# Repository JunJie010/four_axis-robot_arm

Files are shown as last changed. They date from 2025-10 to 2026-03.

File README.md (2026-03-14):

# 基于ESP32的四轴机械臂
>本项目基于**小智&阿奇联合出品 海豚机械臂**开源学习
>
>原项目地址：[机械臂数字孪生项目](https://x509p6c8to.feishu.cn/docx/FeMndRrzRommxGxTkFscJ0zKnKh)
>
>在此感谢原项目作者小智，阿奇的杰出工作
## 项目预览
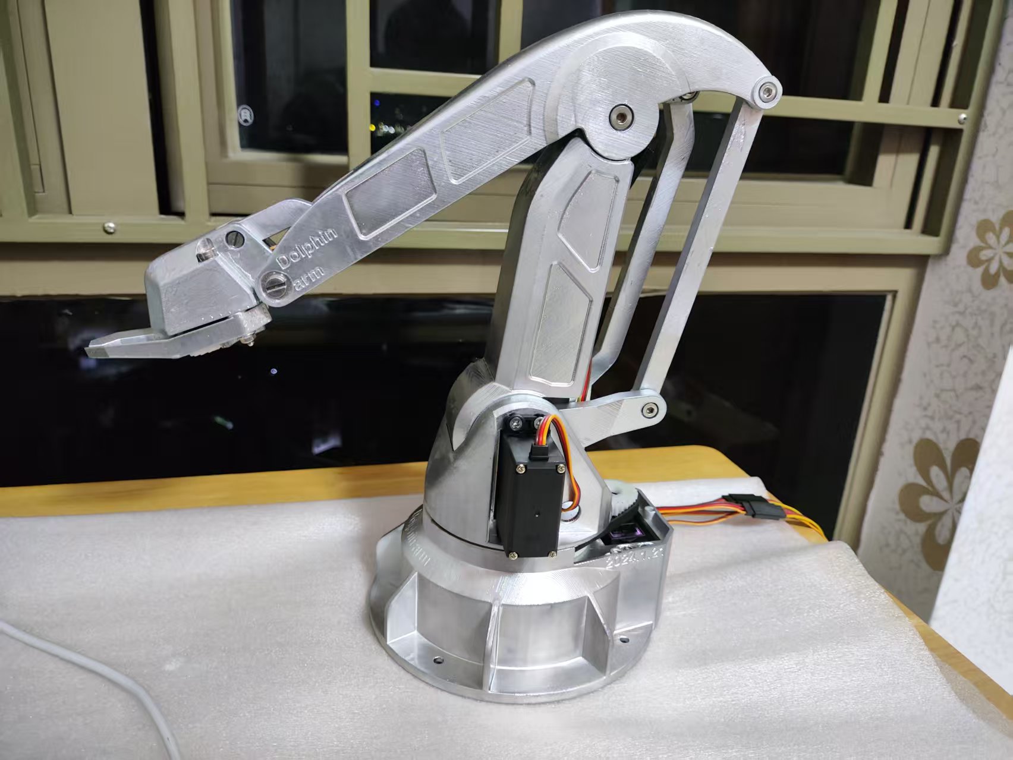
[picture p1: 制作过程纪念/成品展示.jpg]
项目展示

[点击下载项目演示视频](https://github.com/JunJie010/four_axis-robot_arm/blob/main/%E5%88%B6%E4%BD%9C%E8%BF%87%E7%A8%8B%E7%BA%AA%E5%BF%B5/%E6%88%90%E5%93%81%E5%B1%95%E7%A4%BA.mp4)

## 项目功能

- **手机蓝牙遥控**  
  基于 BLE 低功耗蓝牙协议，可通过手机 APP 连接机械臂，实现四轴关节的独立控制和夹爪开合，控制距离满足桌面级应用需求。

- **多舵机协同运动**  
  机身采用 3 个 MG996R 舵机驱动大臂、小臂和底座旋转，夹爪采用 SG90 舵机，通过自定义定时器调度算法实现多舵机同步运动，并可调节转动速度。

- **精确角度控制**  
  基于正逆运动学算法，将机械臂末端位置映射为各关节舵机角度，支持点到点运动控制，可完成指定位置的抓取与释放任务。

- **夹爪抓取功能**  
  夹爪采用双齿轮对称结构设计，最大抓取直径约 3cm，可轻松夹取积木、螺丝等小型物件，夹取力度适中，成功率超过 83%。

- **结构巧妙设计**  
  从零进行机械结构设计，包含固定底座、旋转底座、平行四边形连杆机构和夹爪模块，全部零部件通过 3D 打印制作并手工组装。

## 项目职责
* 设计机械臂结构，包括**固定底座，旋转底座，连杆机构，夹爪机构**
* 3D打印零部件，并进行机械组装
* 绘制主控板，包括**供电，控制器，串口，排针等等**
* 编写机械臂控制代码，包括**舵机驱动代码，蓝牙模块代码**
* 机械臂运动学算法，**正逆运算**
***
## 关于主控板绘制
### 原理图设计如下
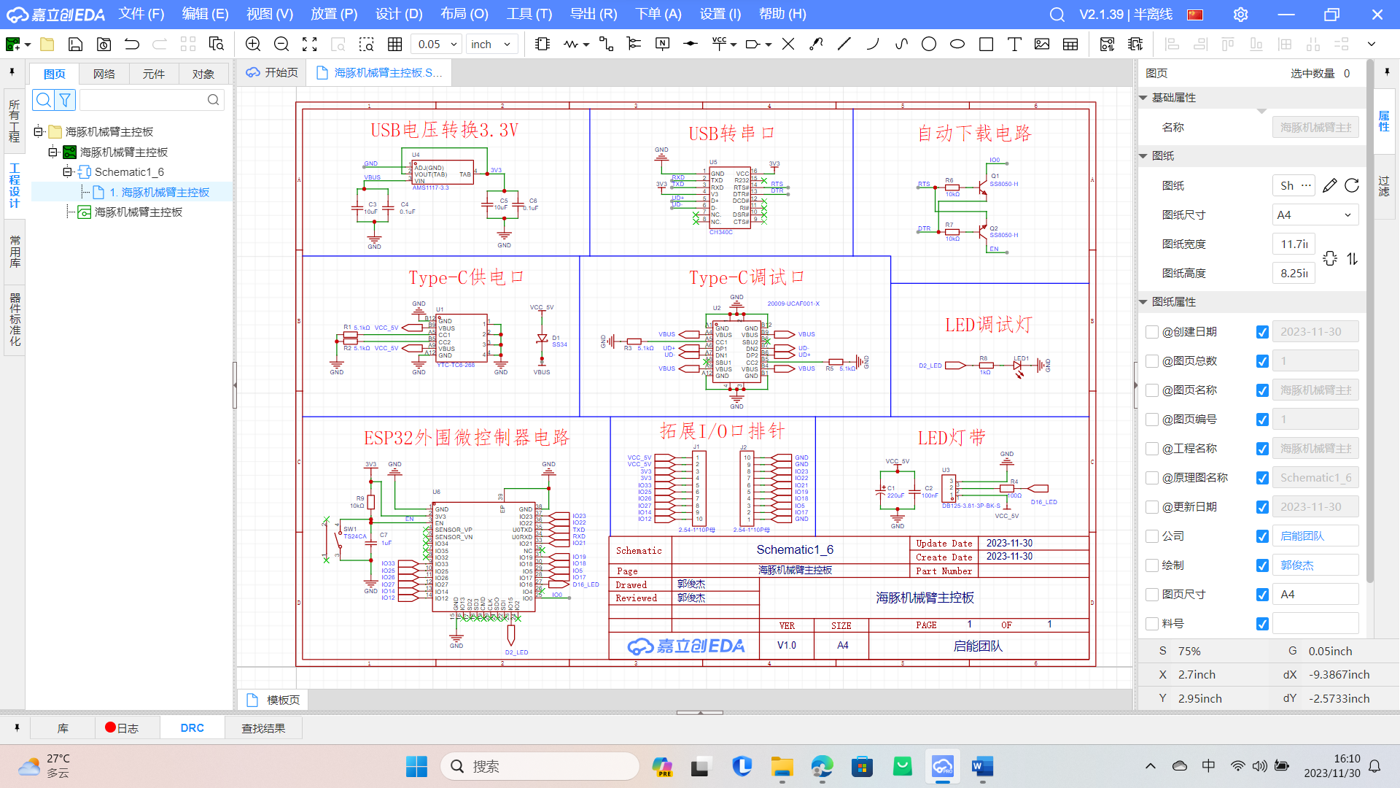
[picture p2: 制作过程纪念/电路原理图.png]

### PCBlayout
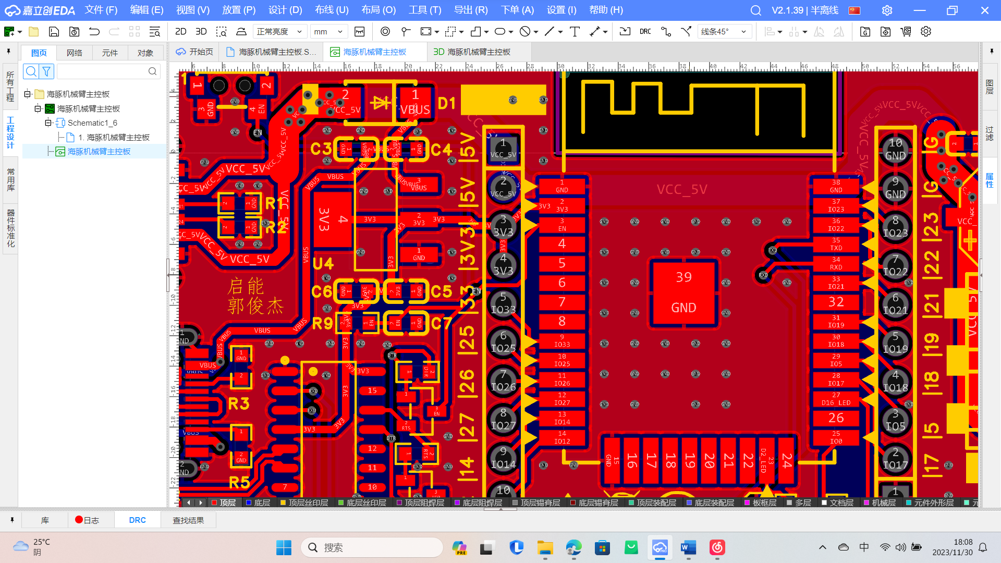
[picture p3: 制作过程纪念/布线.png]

### 板子查看
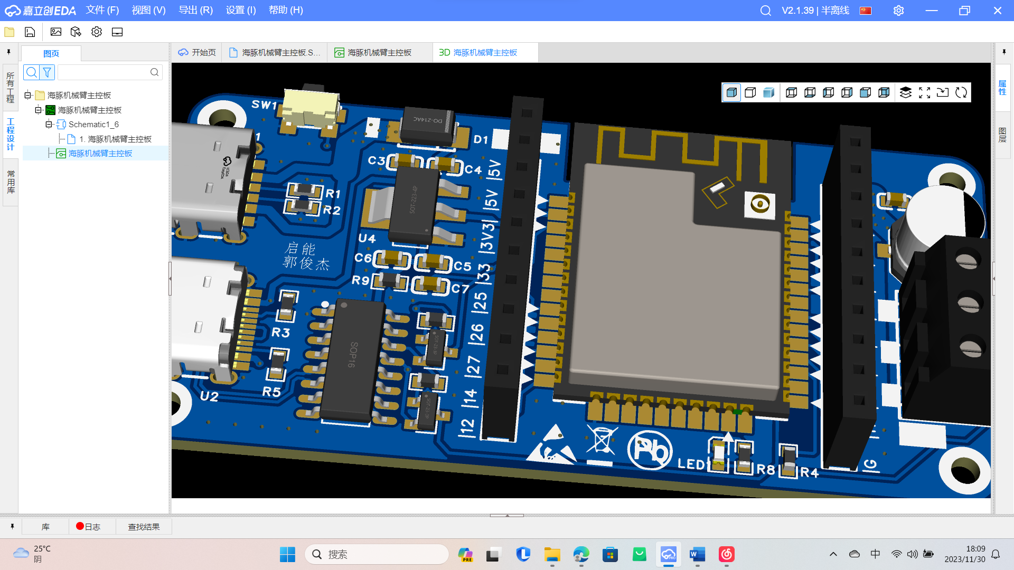
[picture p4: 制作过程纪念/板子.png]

***
## 关于控制代码的编写
编写Arduino，开发环境为VScode，下载PlatformIO插件，用于标准库开发ESP32项目
### 舵机驱动控制
机身采用3个MG996R舵机，夹爪采用SG90舵机，舵机的驱动原理是发送PWM信号，通过改变占空比驱动舵机的转动角度

PWM(Pulse Width Modulation)脉冲宽度调制，在具有惯性的系统中，可以通过一系列脉冲的宽度进行调制，来等效的获得所需模拟参量，常应用于电机控速领域

常用调制方法为通过定时器输出比较功能，通过设置PSC，ARR，CCR寄存器的值来调制一个频率可调，占空比受CCR控制的PWM波形

此处由于引入了ESP32Servo标准库，可以直接用舵机标准库函数对舵机角度进行控制
```      
#include <ESP32Servo.h>               //引入舵机标准库函数

Servo servo;                          //定义舵机变量
servo.setPeriodHertz(50);             //舵机频率初始化函数;
servo.attach(servo_pin,500,2500);     //舵机的初始化参数配置，已对引脚进行配置,参数为引脚，最小微秒，最大微秒
servo.write(45);                      //舵机角度控制函数,参数为舵机角度
//注意，此处只做简单展示，详细代码请看控制代码
```
单舵机的控制较为简单，引入多舵机后需要分别控制各个舵机的角度，可以利用定时器定时功能，每隔一段时间进行一次角度判断函数，当舵机的set和now不同时，舵机转动，并且每转动一次对now加以修正
所以只需要对set值修改就可以驱动舵机转动到相应角度，同时，定时器计时频率可以改变舵机的转动速度，实现多舵机的速度控制
```           
#include <Ticker.h>              //引入定时器功能

struct SERVO                     //定义舵机结构体
{
    Servo engine[4];             //定义舵机变量参数
    uint8_t now[4];              //定义舵机当前角度参数   
    uint8_t set[4];              //定义舵机设置角度参数
};
SERVO servo_engine;              //定义舵机结构体变量
Ticker timer;                    //定义定时器变量

void Servo_Init()                //定义舵机初始化函数，对舵机频率初始化，参数引脚初始化
void Servo_back()                //定义舵机归位函数，机械设计时设计每个舵机的初始值，上电后自动执行复位功能
void timer_speed(uint8_t x)      //舵机速度控制函数，原理是利用定时器定时功能，每隔一段时间进行一次角度判断函数
void timer_back()                //定义舵机now修正函数，在舵机运动到指定位置后，修正now为当前值，避免一直运动
uint8_t Servo_run(uint8_t x,uint8_t set_angle,uint8_t now_angle)         //定义舵机驱动函数，当set和now不同时，舵机驱动
void Servo_motor_run(uint8_t a,uint8_t b,uint8_t c,uint8_t d)         //定义多舵机控制函数，给set值
//注意，此处只做简单展示，详细代码请看控制代码
```
### 多舵机控制
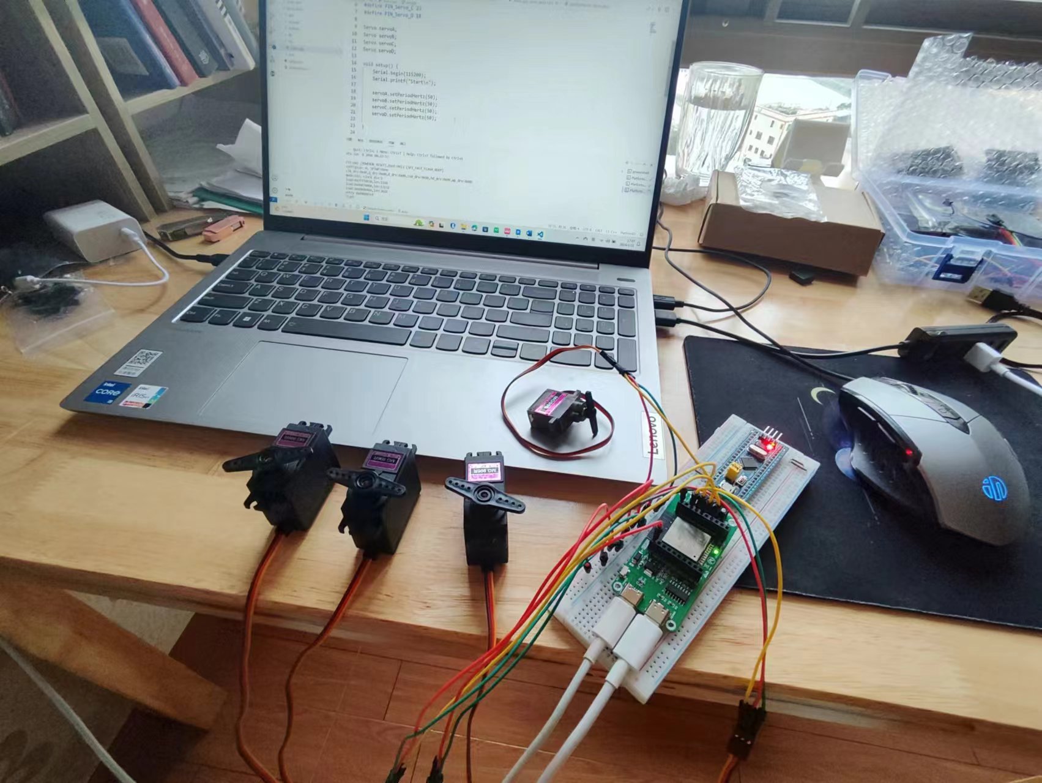
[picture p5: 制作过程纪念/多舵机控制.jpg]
舵机控制

### 蓝牙模块编写
采用蓝牙模块，由于项目与控制端距离近，控制方便简单，故此处采用BLE(低功耗蓝牙)
在BLE通信模式中，存在两类设备：BLE服务端和BLE客户端，通信时，BLE服务端向外发送信号，可以被附件BLE客户端发现，一个BLE客户端可以连接特定的服务端，然后读取服务端发送的信号数据
BLE不但支持点对点传输，还支持广播模式，还可以组建Mesh网络
```
#include <BLEDevice.h>
#include <BLE2902.h>              //引进相关蓝牙通讯协议

#define SERVICE_UUID "4fafc201-1fb5-459e-8fcc-c5c9c331914b"
#define CHARACTERISTIC_UUID "beb5483e-36e1-4688-b7f5-ea07361b26a8"       //完整的128位UUID码

BLECharacteristic *pCharacteristic = NULL;            //创建特征Characteristic
bool bleConnected = false;                            //定义布尔型变量用于判断蓝牙是否连接

class bleServerCallbacks : public BLEServerCallbacks                     //Server回调函数声明，并用串口打印设备的连接状况
class bleCharacteristicCallbacks : public BLECharacteristicCallbacks      //客户端回调函数声明，用于客户端读取事件和写入事件
void BLE_Init()                   //定义初始化蓝牙函数，创建BLE蓝牙设备，创建服务器，设置设备的模式为BLE Server，创建服务，启动服务并开启广播
//注意，此处只做简单展示，详细代码请看控制代码
```
### 手机蓝牙控制
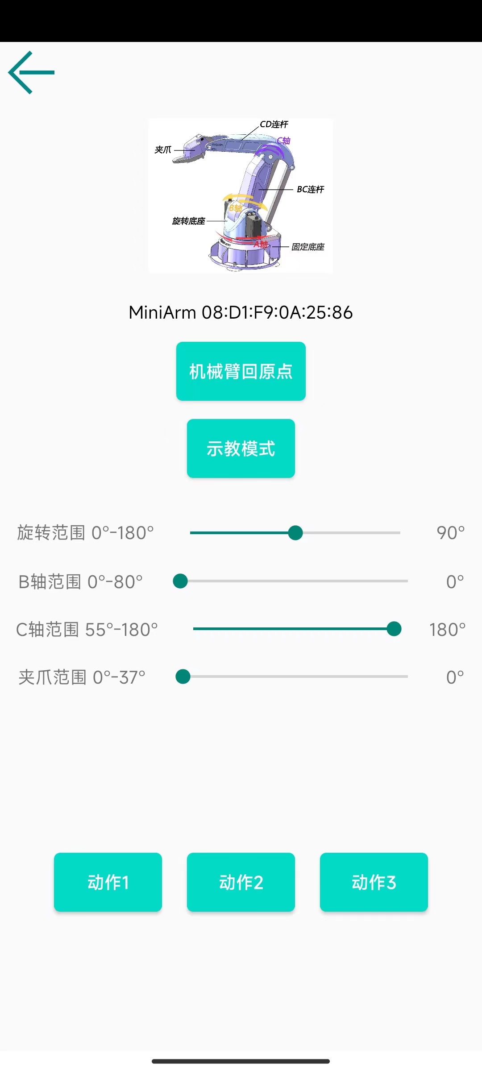
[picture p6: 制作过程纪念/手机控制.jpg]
蓝牙编写

***
## 关于运动学算法
由于机械臂机械设计结构原因，舵机无法实现自由转动，受到结构限制

此处采用正逆运算解决运动学问题，正向运动学：给定机器人各关节变量，计算机器人末端的位置姿态，逆向运动学：已知机器人的末端位置姿态，计算机器人各关节的变量
假设各轴角度为A,B,C,D；各舵机角度为A_,B_,C_,D_；

通过机械结构和正逆运算，得到以下结论
>A轴：
>
>0 < A_ < 180; 0 < A < 70; A = A_ / (72/28)
>
>B轴：
>
>0 < B_ < 80; 0 < B < 80; B = B_
>
>C轴：
>
>140 - B_ < C_ < MIN(180,196-B_); 43.5 < C < MIN(83.5,95.5); C = B + C_ -96.5
>
>D轴：
>
>0 < D_ < 37.5; 0 < G < 29; G = G_/(22/17)

***
## 关于结构设计
逆向工业型机械臂ABB-irb-460，得出机械臂运动原理，是由两个平行四边形的连杆机构使得D轴始终与地面垂直，确定了设计框架
### 逆向工程
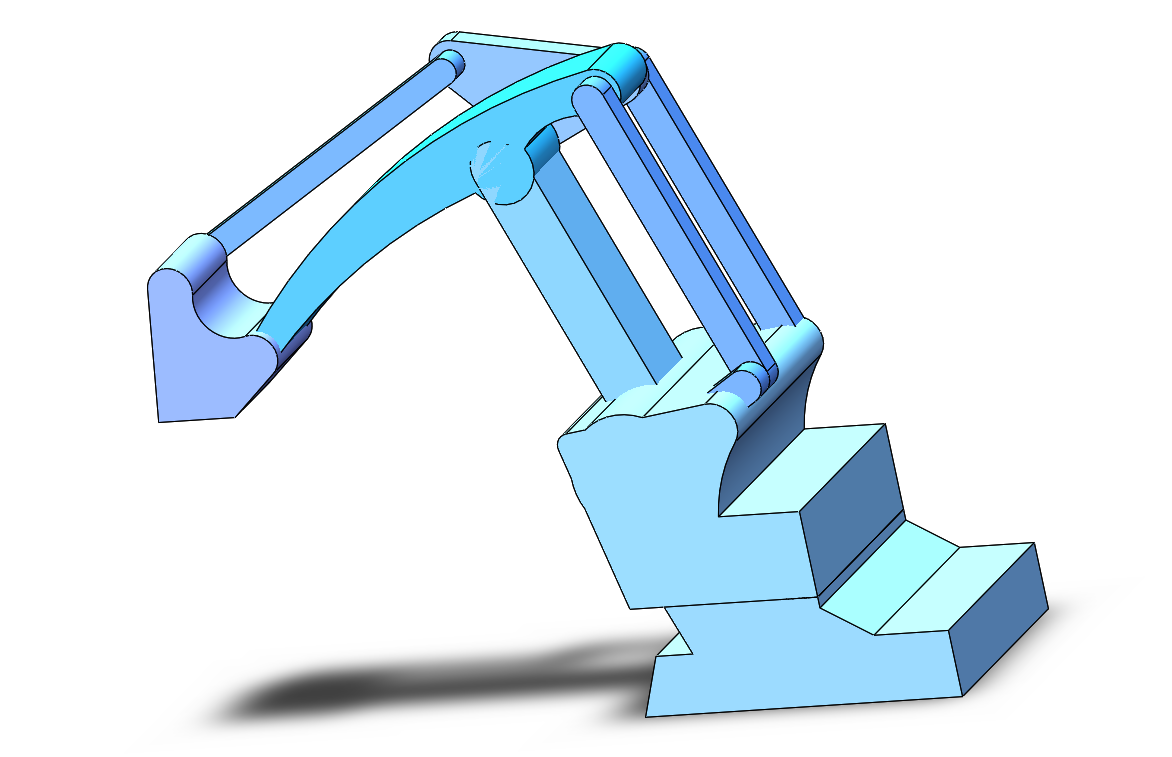
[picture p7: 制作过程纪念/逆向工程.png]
逆向工程

### 平行四边形法则
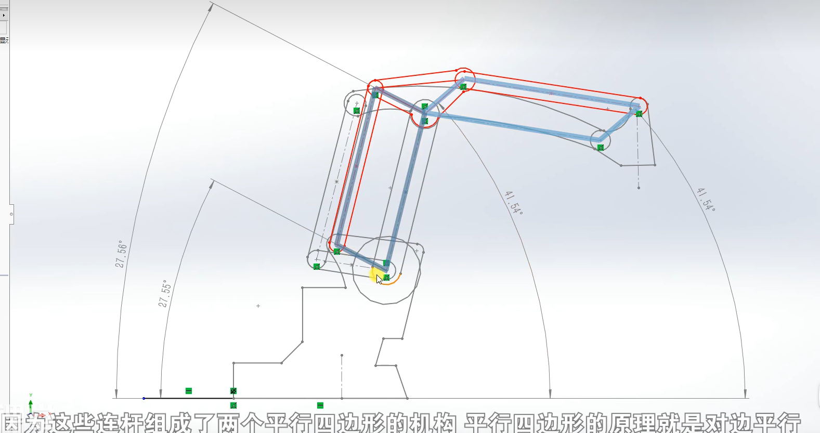
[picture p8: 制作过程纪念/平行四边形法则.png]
机械原理

### A轴 固定底座设计
>**需求：**
>
>旋转机构，将舵机安装在固定底座内，设计它们之间的驱动，考虑如何将舵机线通过A轴
>
>**解决：**
>
>轴承的外圈固定在固定底座上，轴承的内圈与旋转底座相连；
>大同步带轮与小同步带轮之间通过同步带驱动；
>用轴间螺丝，防松螺母将两个轴承连接起来；
>在大轴承的内部设计一个过线孔；
>
### A轴 固定底座预览
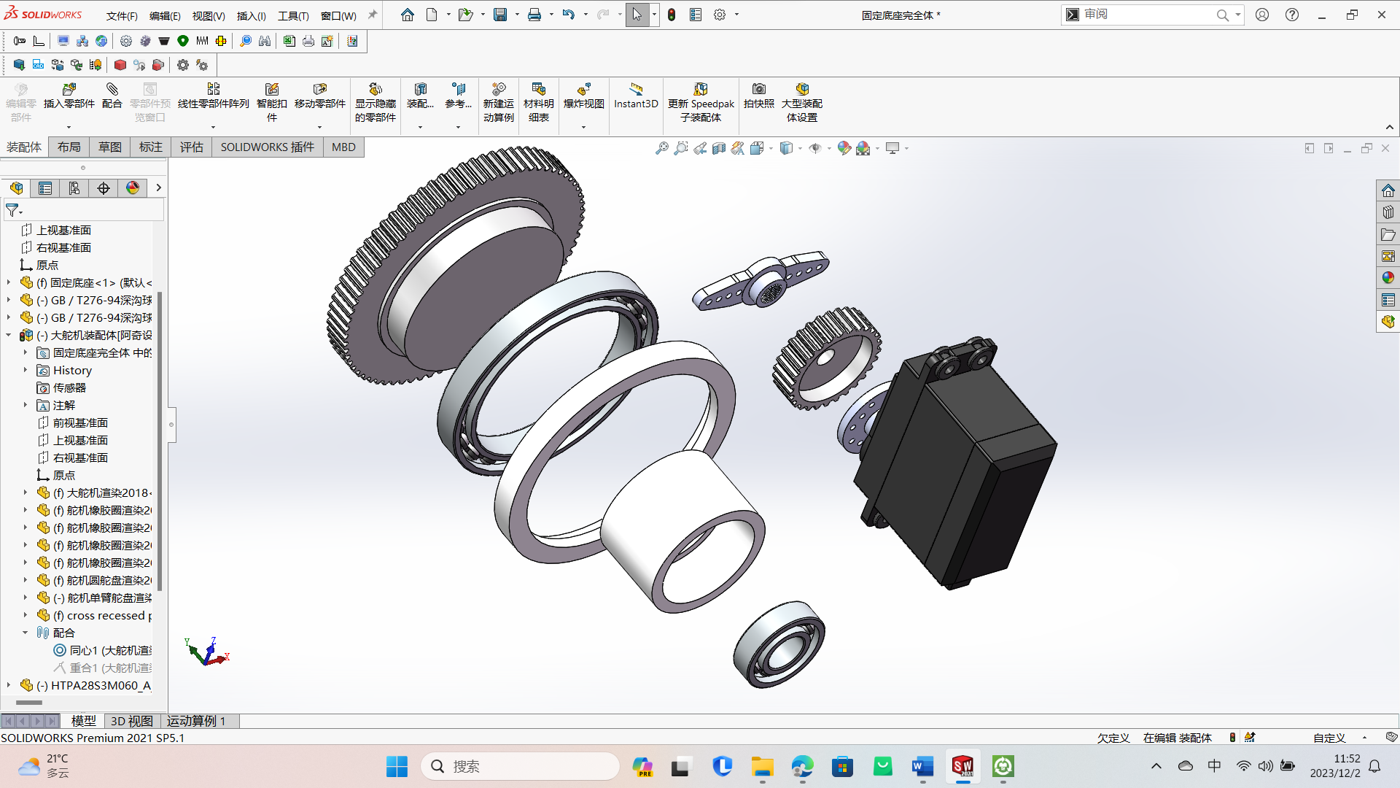
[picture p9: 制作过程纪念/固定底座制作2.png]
固定底座

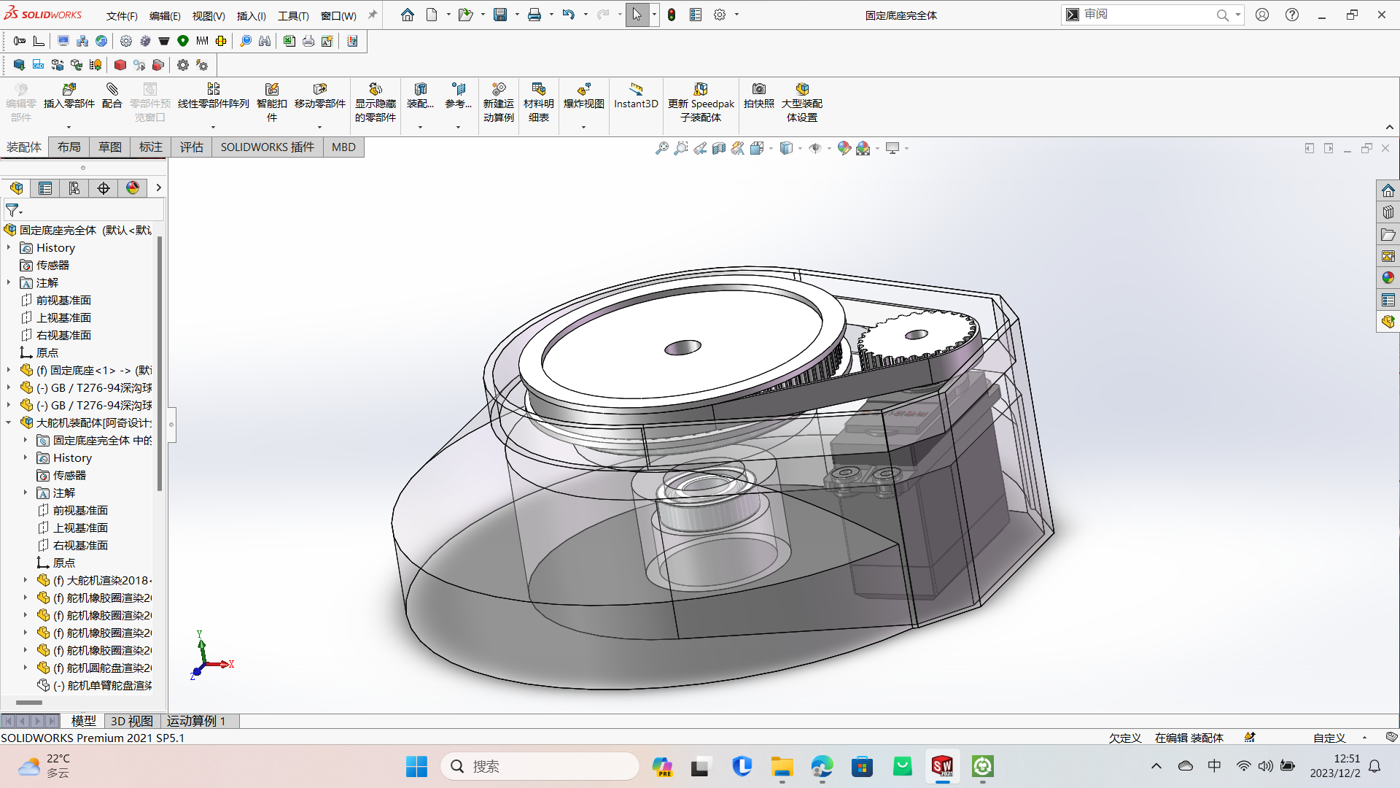
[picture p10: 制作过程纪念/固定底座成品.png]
固定底座

### B轴 旋转底座设计
>**需求：**
>
>旋转底座与固定底座连接，舵机如何驱动BC连杆与C轴连杆，BC连杆与C轴连杆的旋转机构，舵机如何安装
>
>**解决：**
>
>采用螺丝或螺母连接；
>C轴摇杆驱动，圆舵盘直连；
>BC连杆驱动需要一定的刚性，设计为一字舵盘连轴器；
>深沟球轴承，螺丝与螺母固定，BC连杆采用双臂结构以增加刚性；
>
### B轴 旋转底座预览
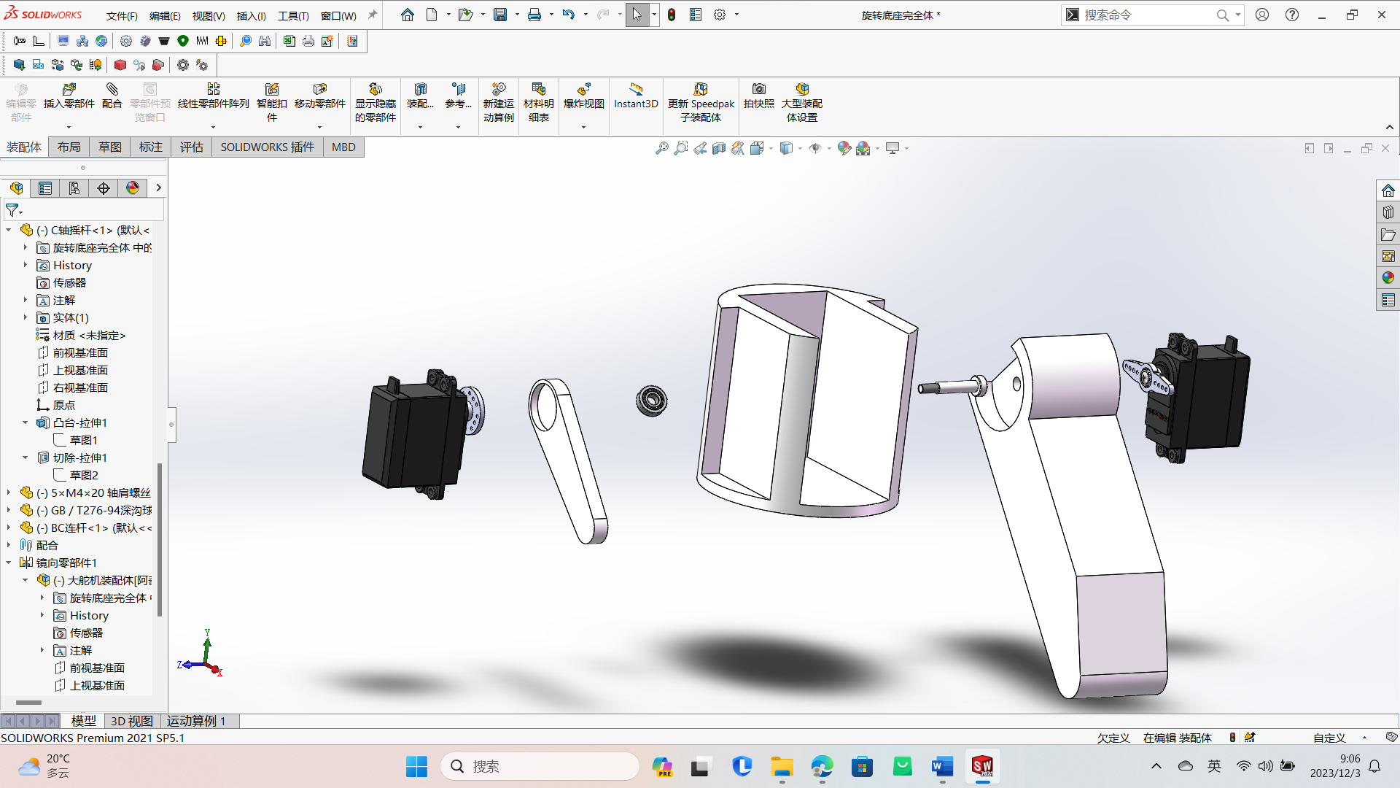
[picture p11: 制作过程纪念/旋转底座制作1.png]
旋转底座

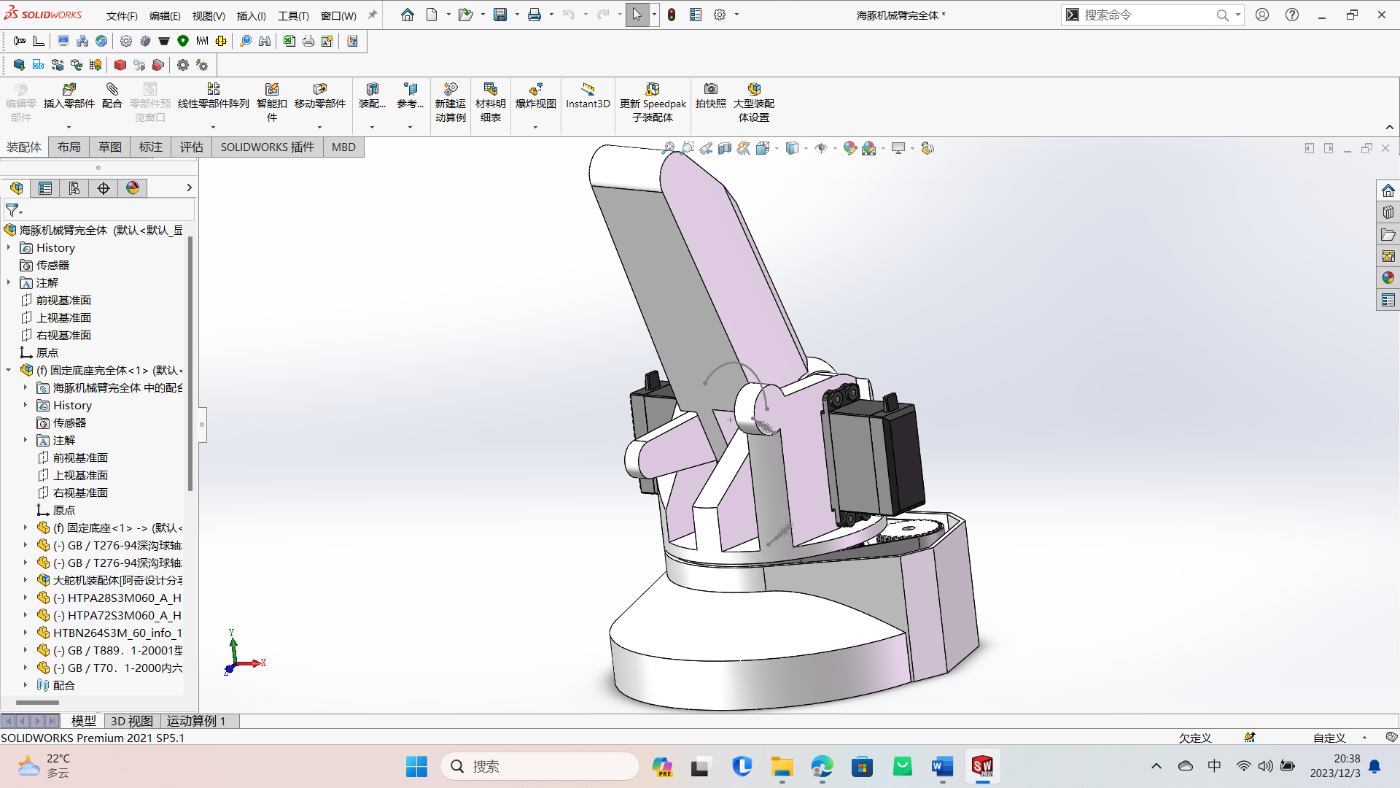
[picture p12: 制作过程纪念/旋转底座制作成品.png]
旋转底座

### 旋转底座中枢机构比较复杂，容易报错，需细心处理
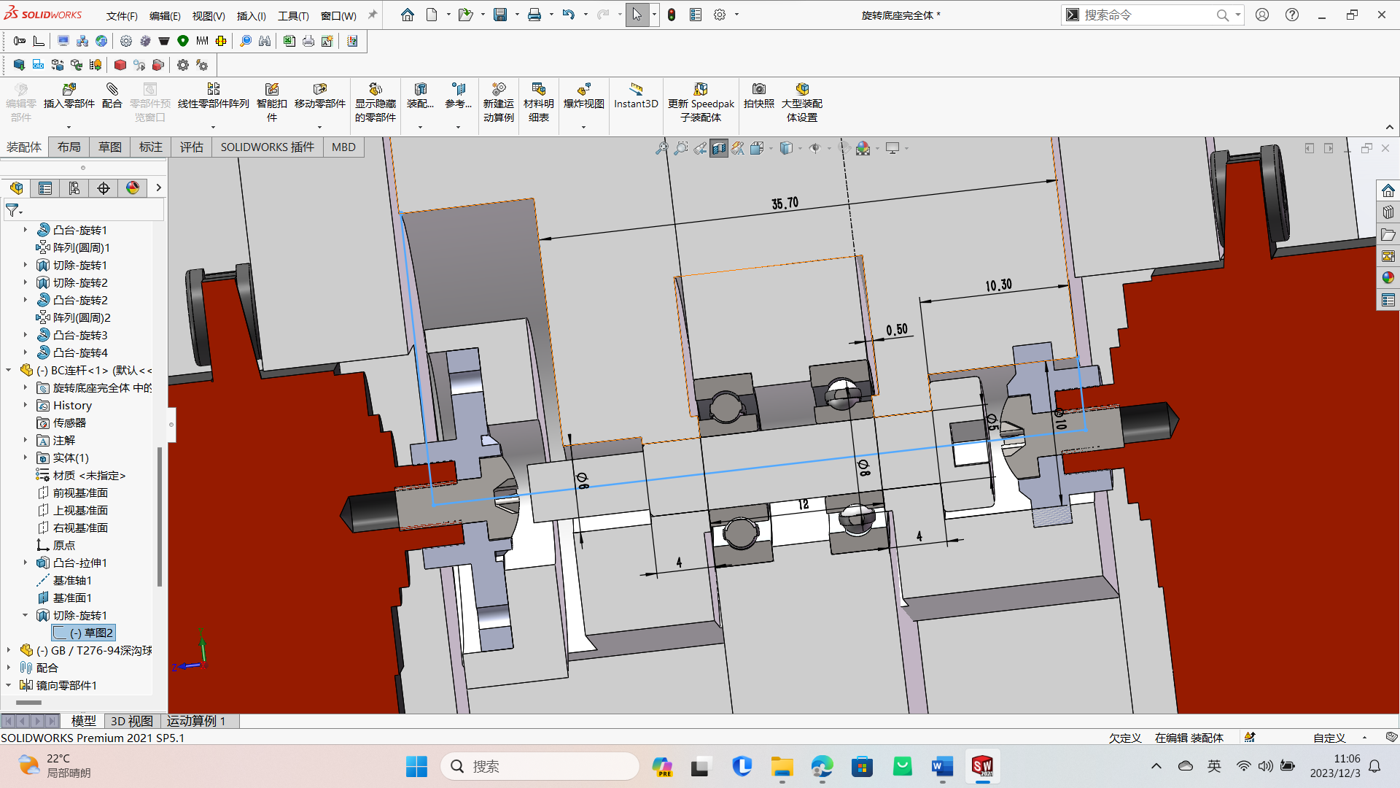
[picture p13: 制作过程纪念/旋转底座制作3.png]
旋转底座

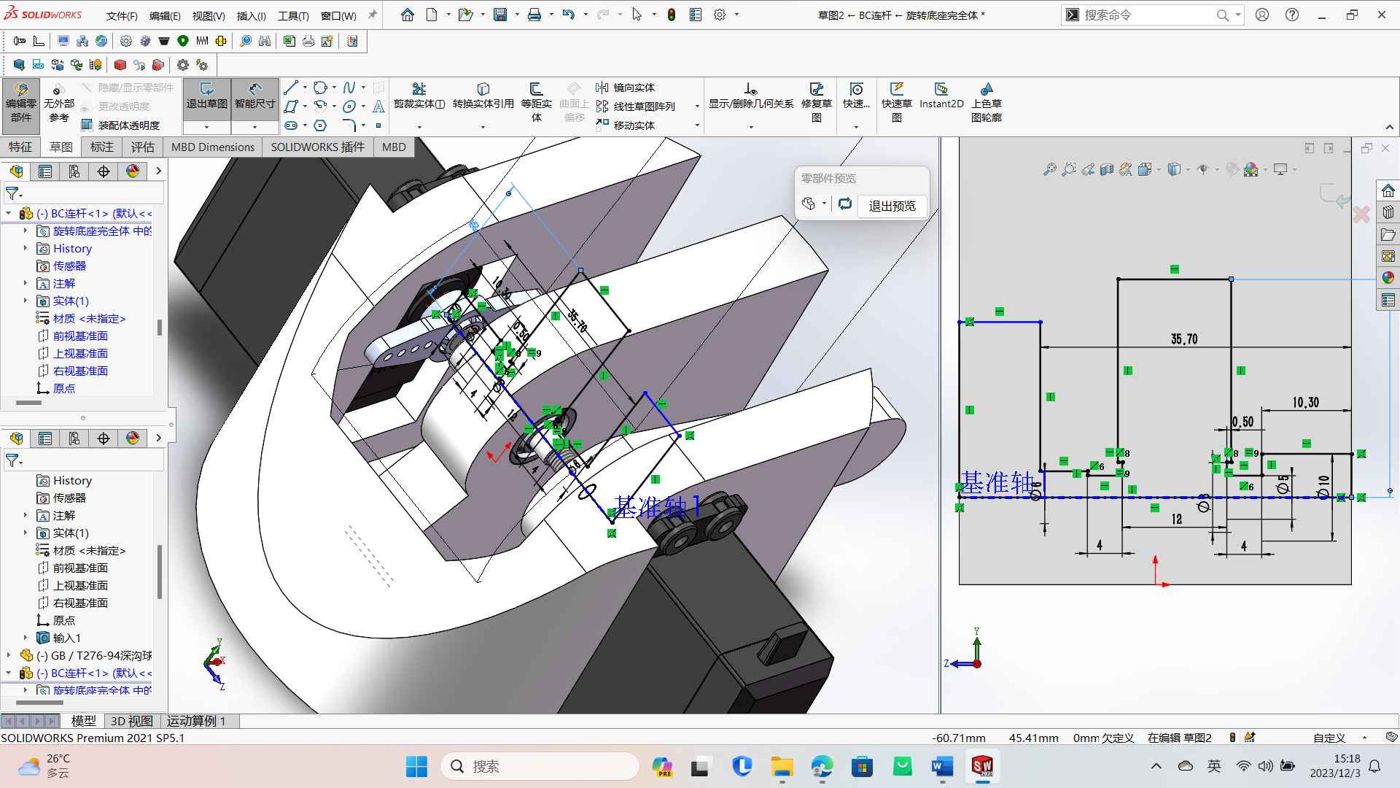
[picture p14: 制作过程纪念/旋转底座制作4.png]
旋转底座

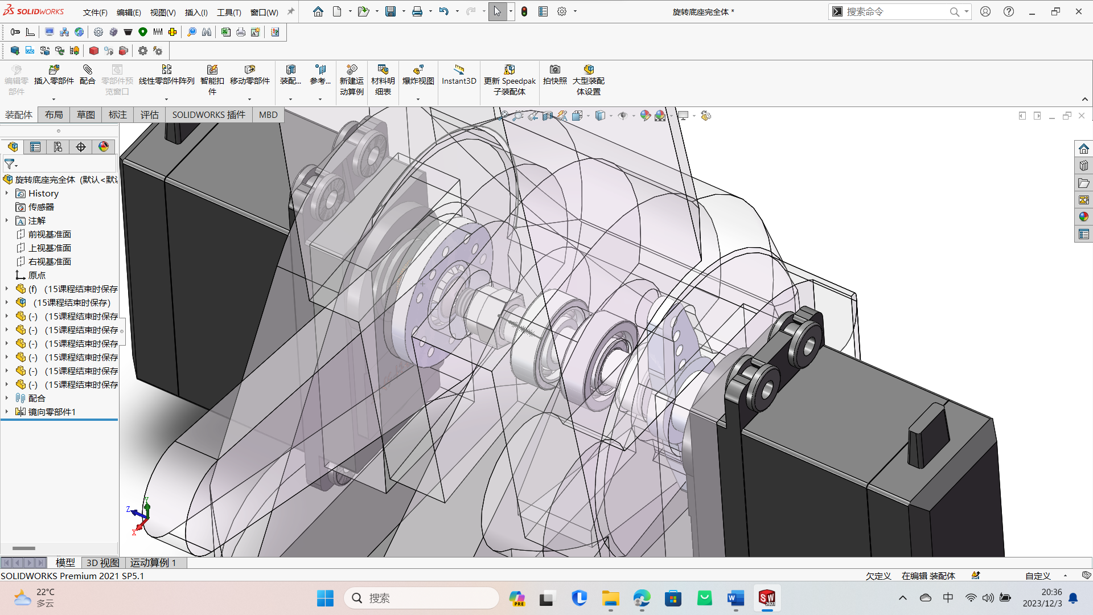
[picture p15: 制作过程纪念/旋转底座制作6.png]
旋转底座

### C轴部分 连杆机构
>**需求：**
>
>CD连杆，三角形连杆的外形尺寸，C轴机构的设计，BC，CD，三角形连杆之间的配合，连杆之间的旋转机构
>
>**解决：**
>
>采用平行四边形结构
>
### C轴 连杆机构预览
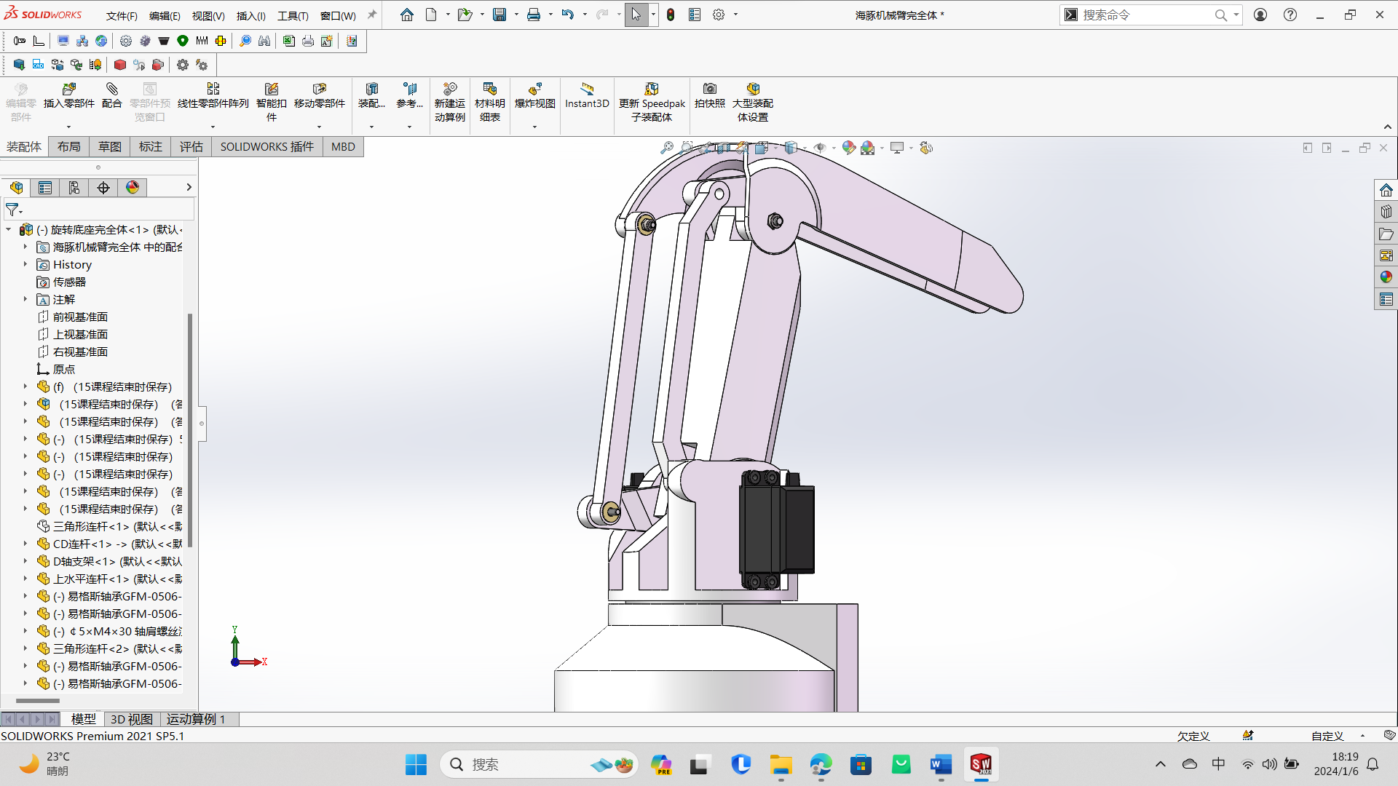
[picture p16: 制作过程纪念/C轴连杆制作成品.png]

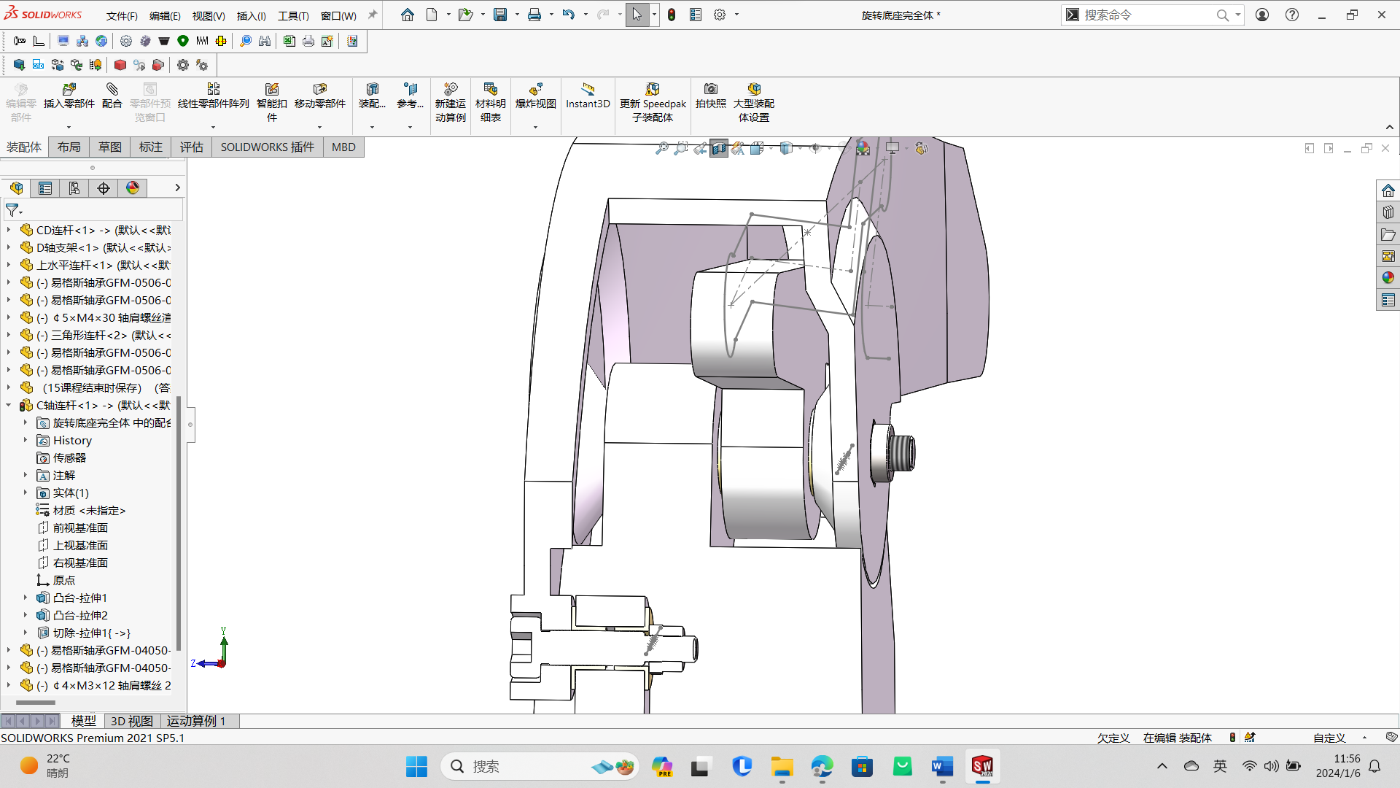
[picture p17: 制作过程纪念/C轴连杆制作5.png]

### 连杆机构中枢机构比较复杂，容易报错，需细心处理
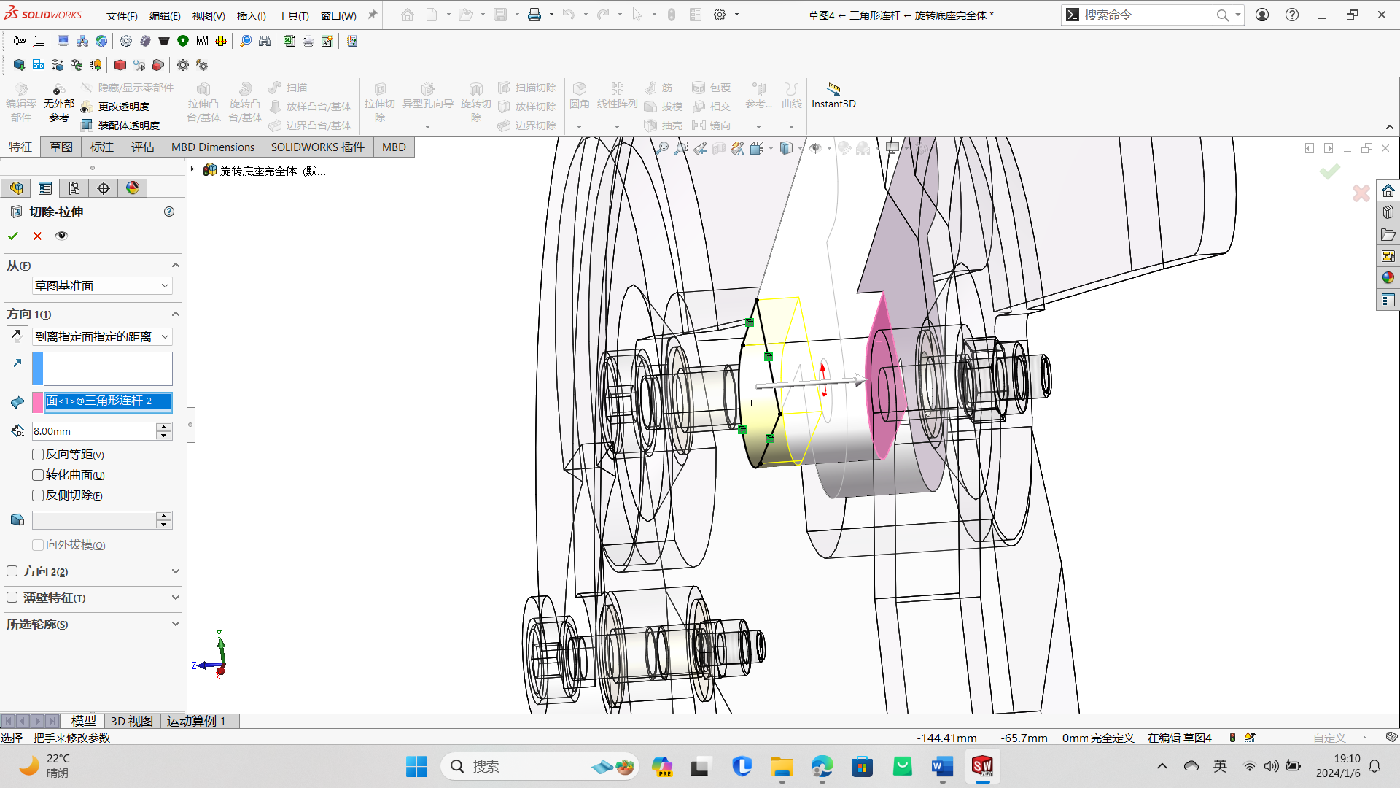
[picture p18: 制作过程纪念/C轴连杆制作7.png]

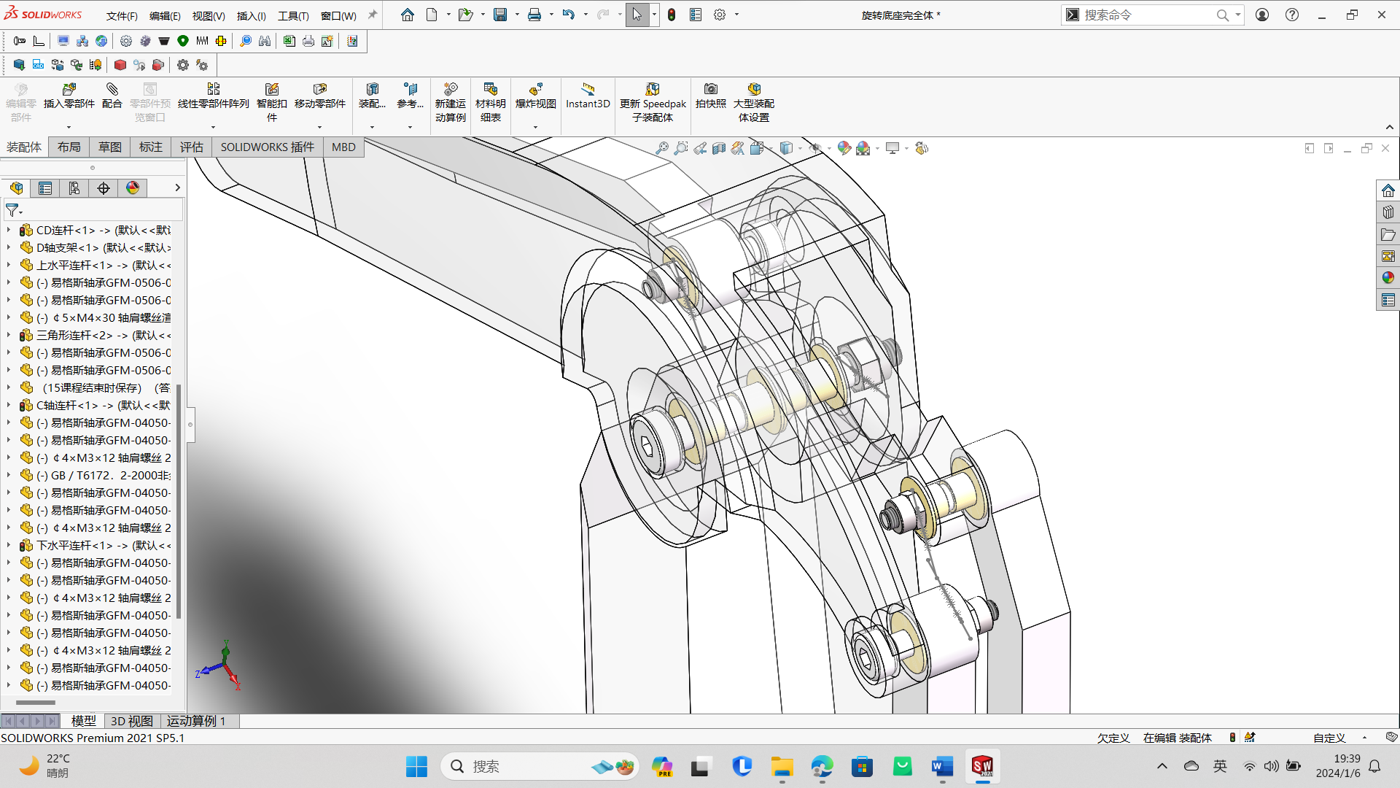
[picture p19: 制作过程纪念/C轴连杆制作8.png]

### D轴部分 夹爪机构
>**需求：**
>
>夹爪与CD连杆，上水平连杆之间的连接，能夹取一些放置在桌面的小物品，能夹多大的，夹取动作结构，动力来源
>
>**解决：**
>
>动力来源采用双齿轮结构；
>夹取方式为旋转手指，对称结构；
>夹取直径大概3cm左右；
>
### D轴部分 夹爪机构预览
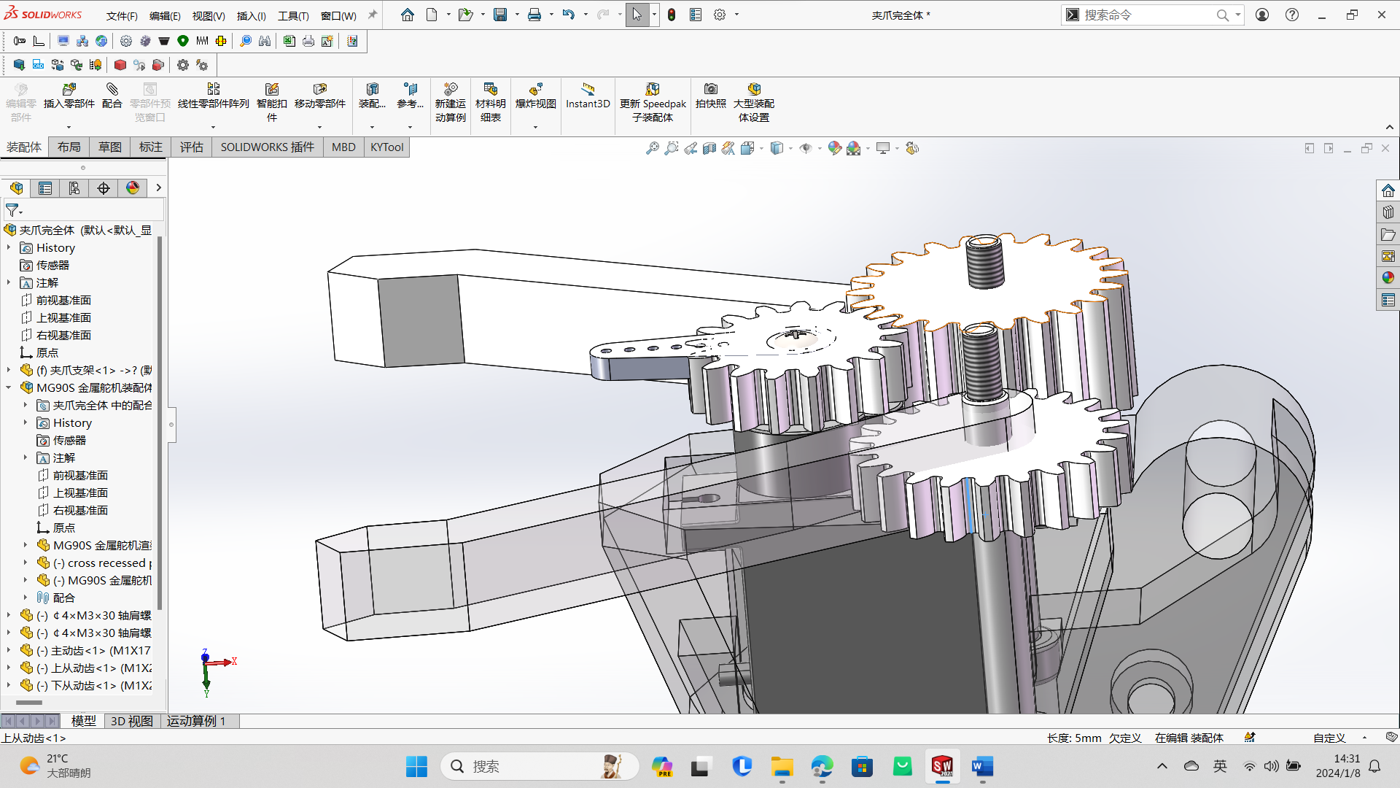
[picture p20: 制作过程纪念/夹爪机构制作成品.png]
夹爪机构

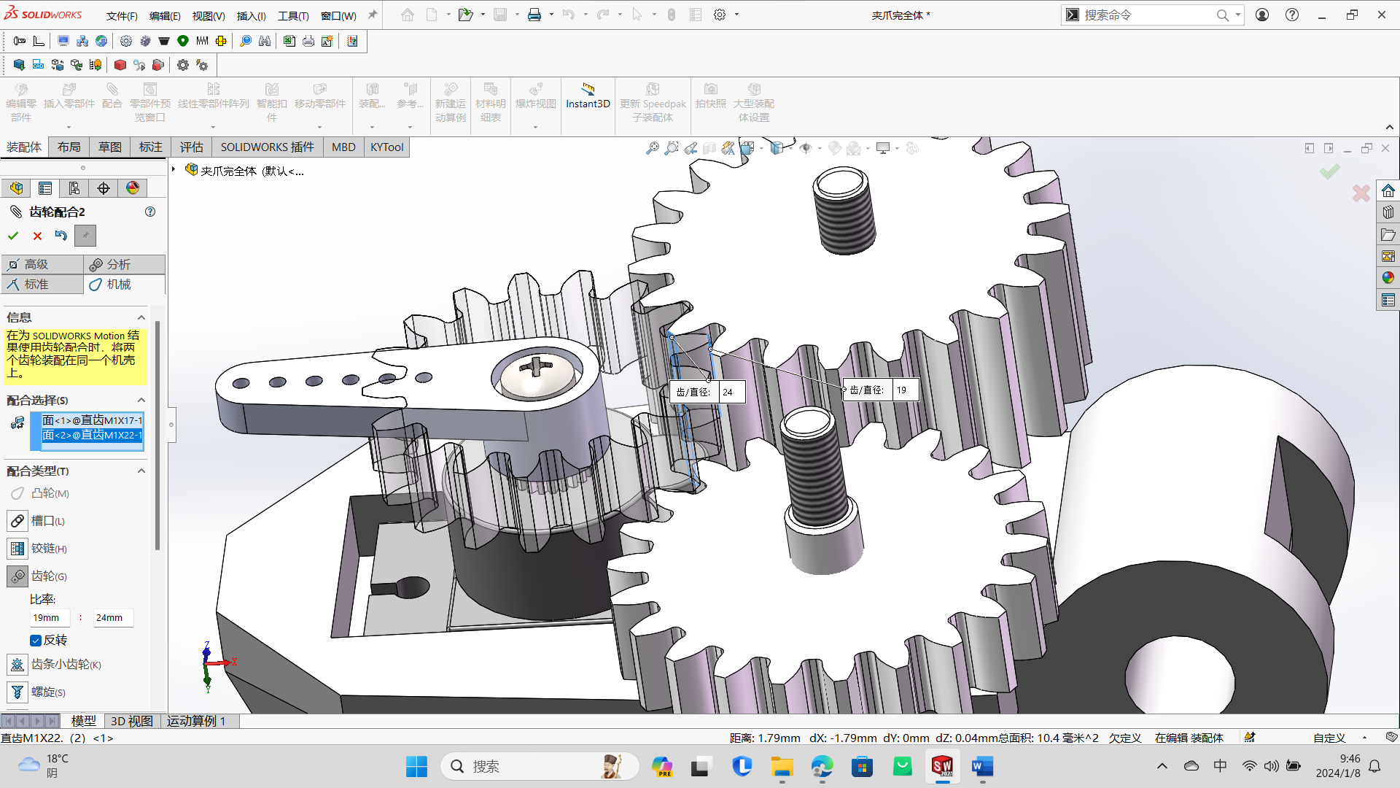
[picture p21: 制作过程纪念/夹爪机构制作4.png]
夹爪机构

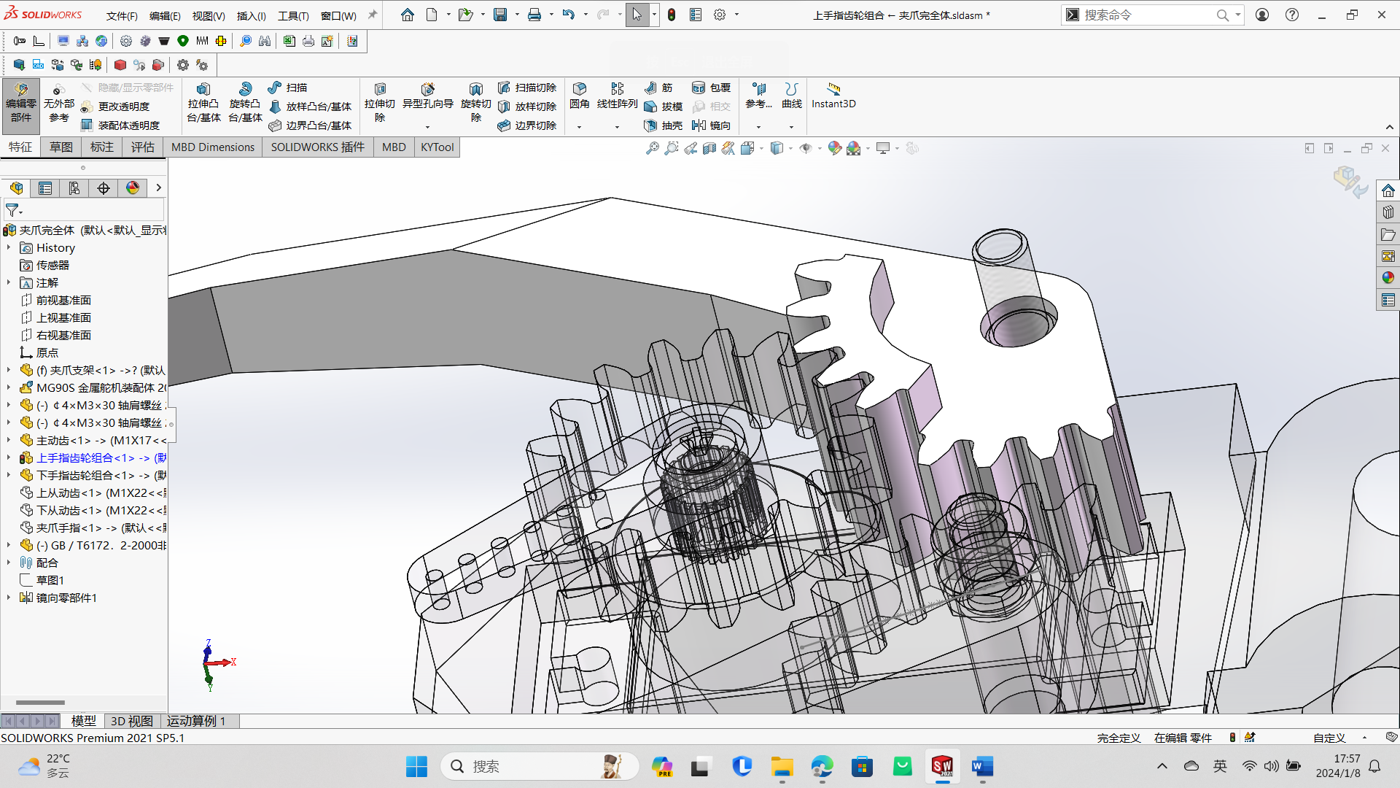
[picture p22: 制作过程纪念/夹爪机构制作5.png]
夹爪机构

***
## 关于机械组装
通过以上的机械设计，再进行一些细节优化后，四轴机械臂的完全体组装完毕
### 机械臂完全体
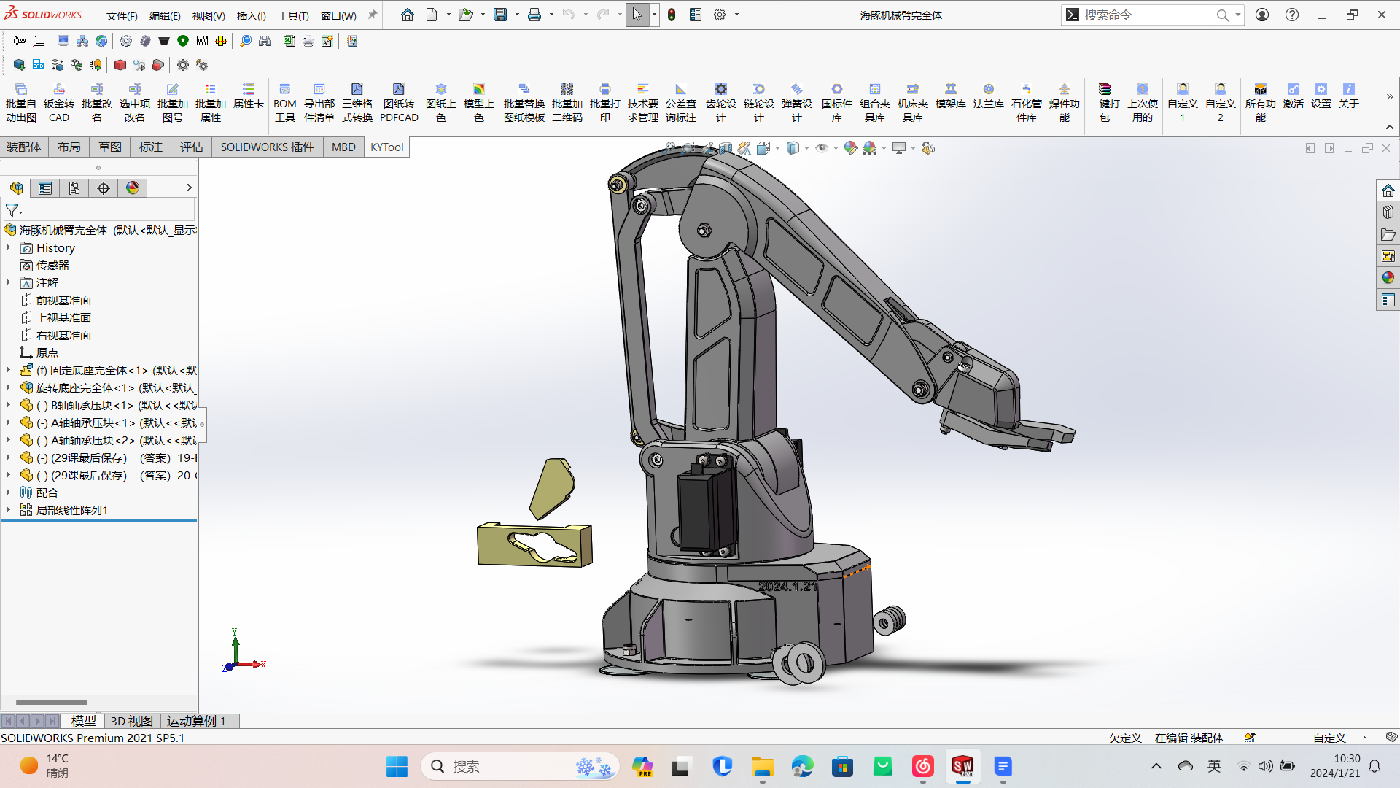
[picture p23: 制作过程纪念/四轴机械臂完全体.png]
四轴机械臂

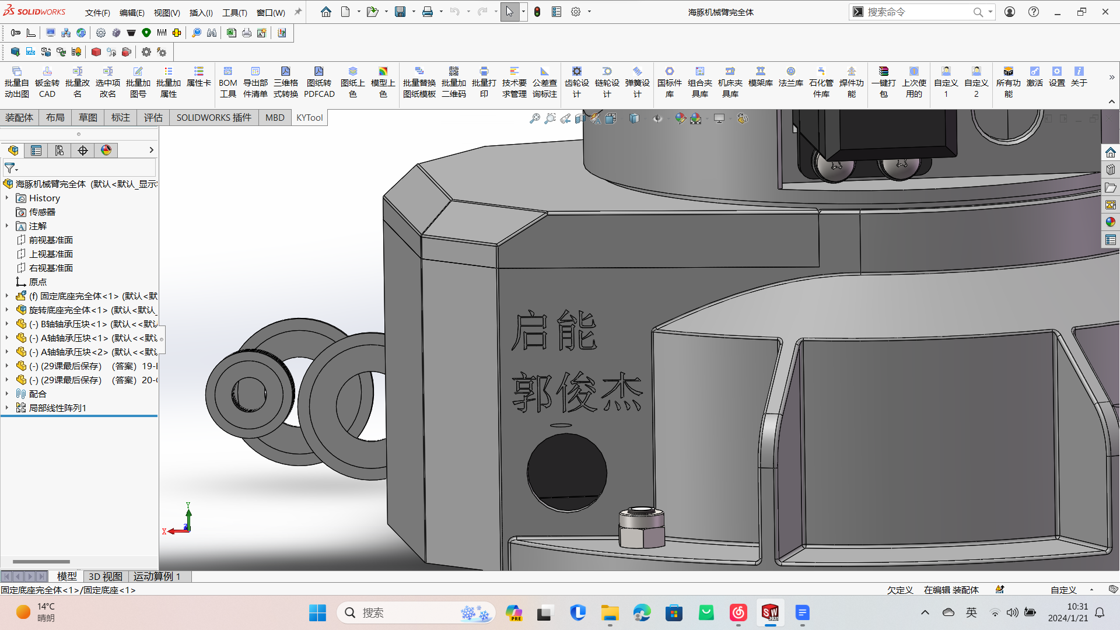
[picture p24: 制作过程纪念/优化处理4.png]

紧接着，导出四轴机械臂装配体零部件
### 机械臂装配体零部件
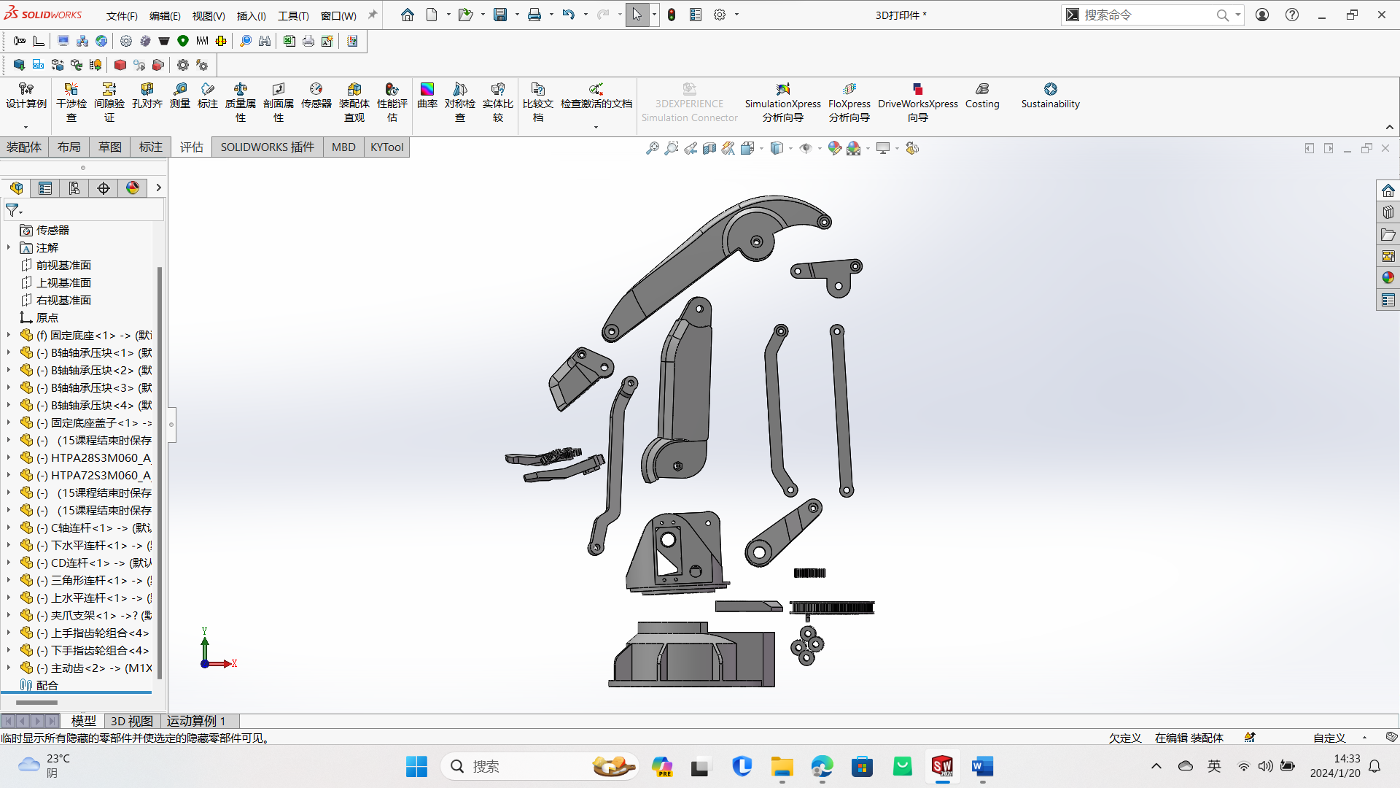
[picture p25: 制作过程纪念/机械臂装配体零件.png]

3D打印后，进行手动喷漆，组装
### 机械臂手动组装
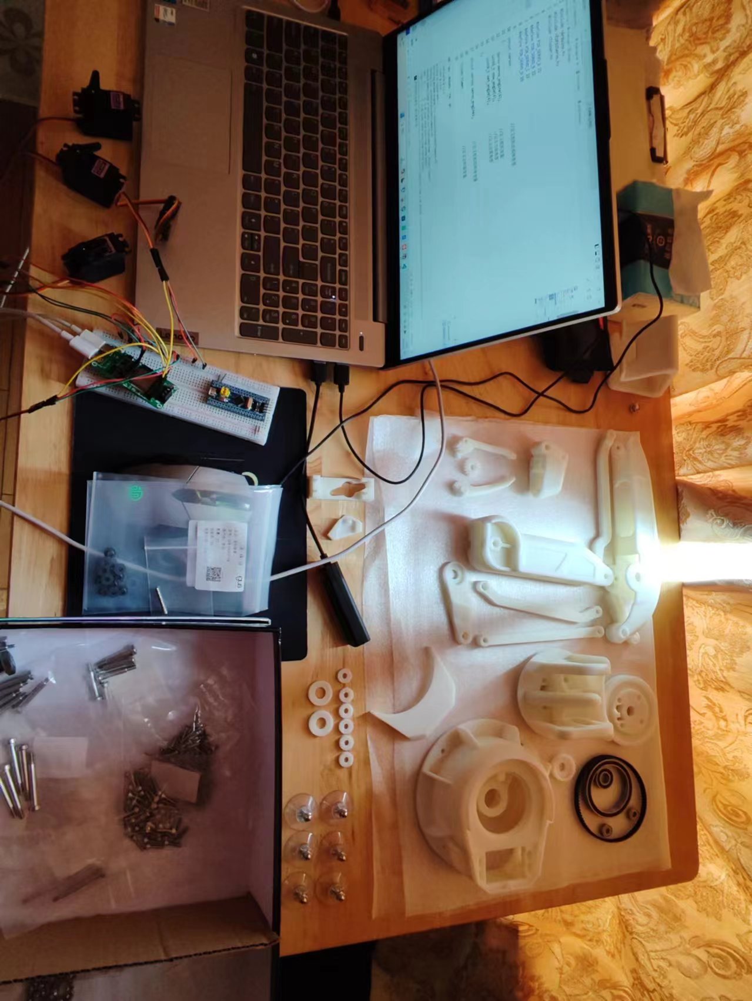
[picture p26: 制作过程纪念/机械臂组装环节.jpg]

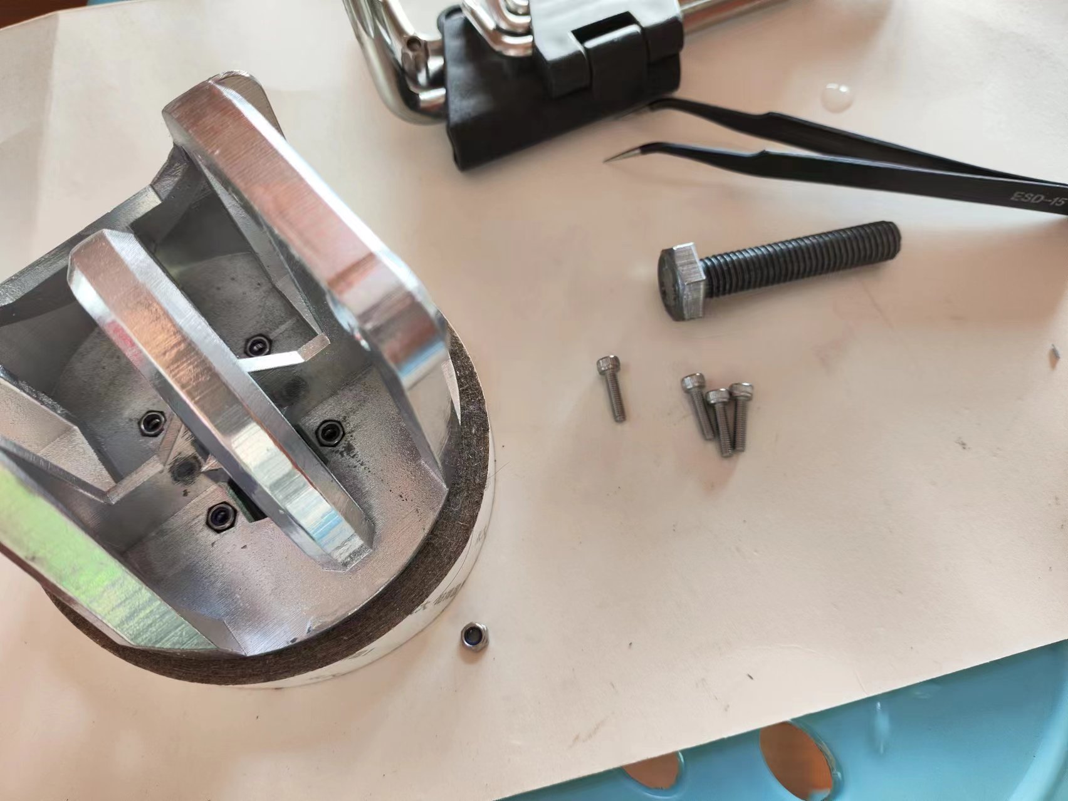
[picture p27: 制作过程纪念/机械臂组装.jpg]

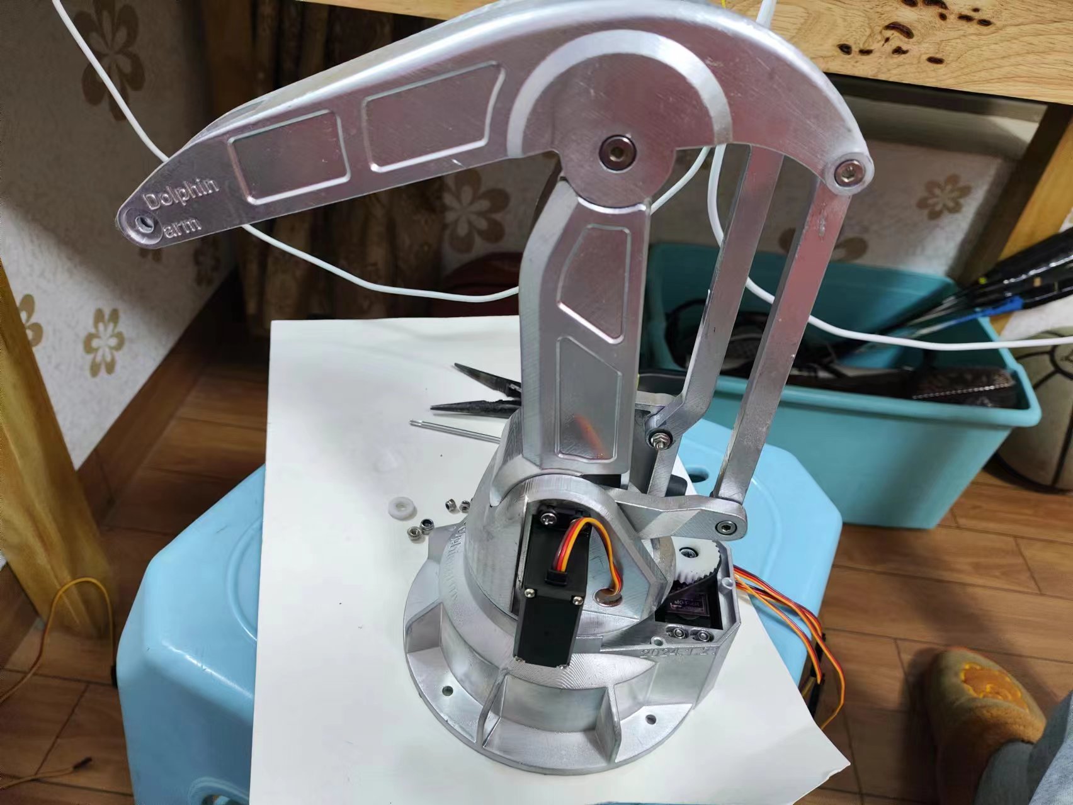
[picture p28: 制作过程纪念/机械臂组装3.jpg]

***

>再次感谢原项目作者小智，阿奇的杰出工作
>
>同时也欢迎大家一起来学习
>
***
后面会继续更新，请等待...

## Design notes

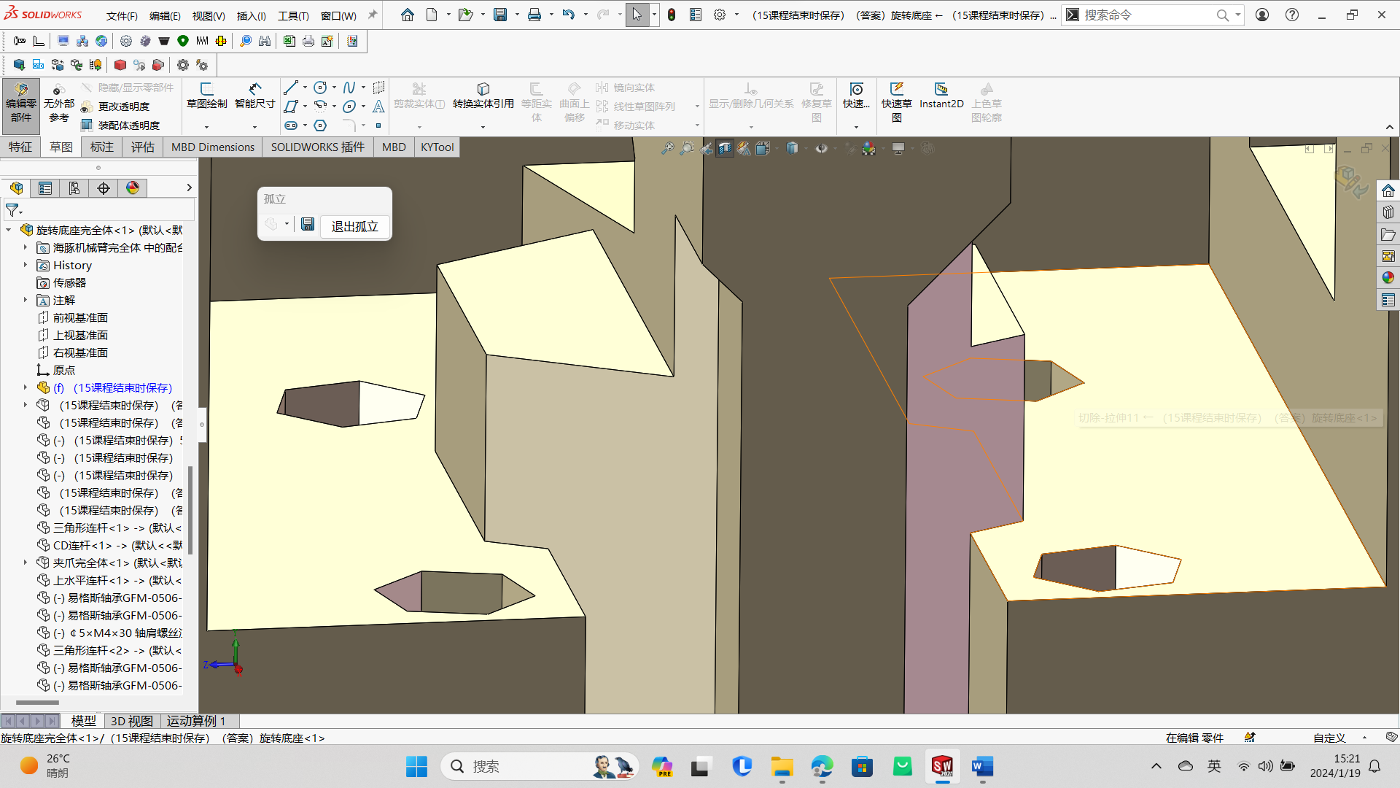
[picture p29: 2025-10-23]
制作过程纪念/优化处理3.png

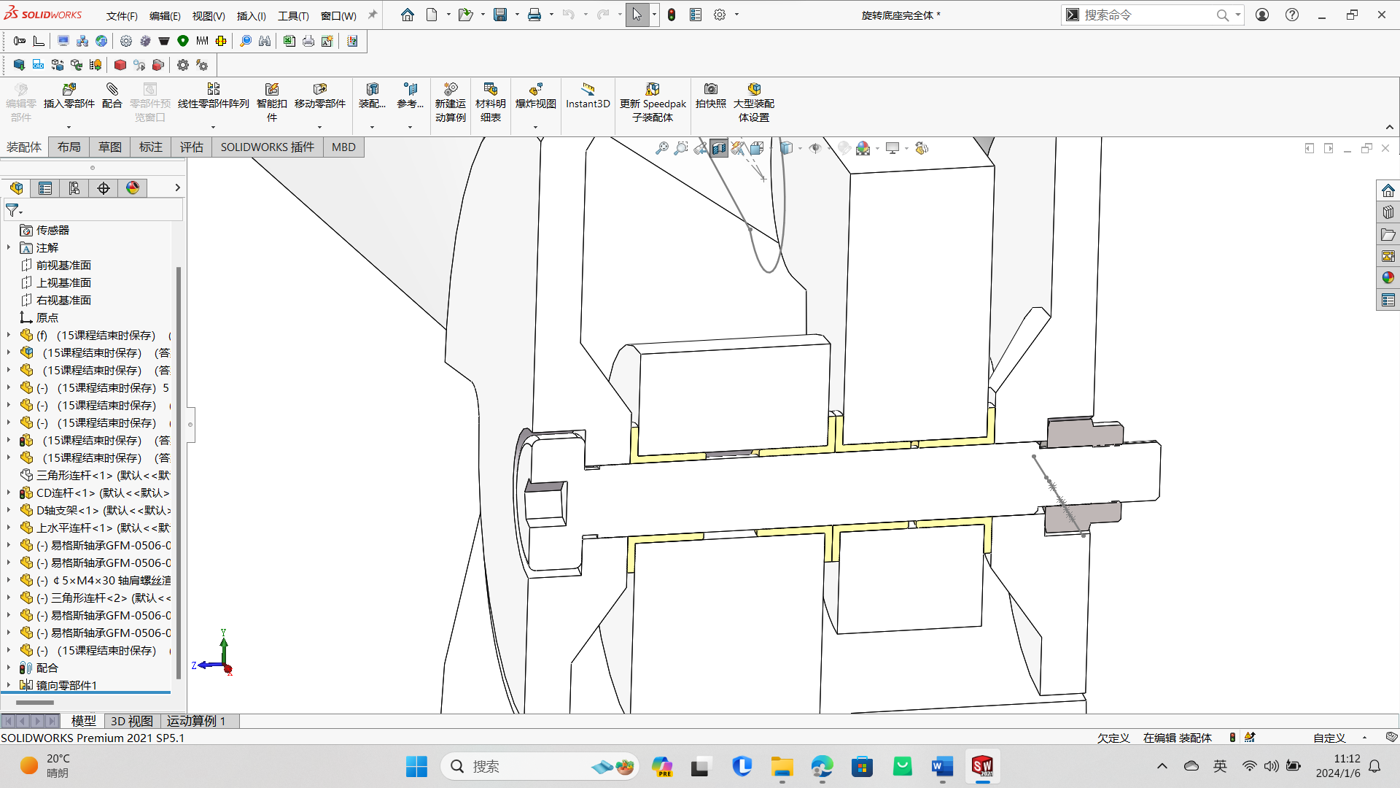
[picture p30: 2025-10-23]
制作过程纪念/C轴连杆制作4.png

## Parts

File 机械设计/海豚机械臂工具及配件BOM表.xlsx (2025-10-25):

海豚机械臂项目标准件配件BOM表 |  |  | 海豚机械臂项目工具表
名称 | 参数 | 数量 | 名称 | 参数
深沟球轴承 | 61809 | 1 | 螺丝刀组合 | 标配
 | 61900 | 1 | 老虎钳 | 5寸
 | 695ZZ | 2 | 胶水 | 502
同步带 | STS 264-S3M-B6 | 1 | 喷漆 | 银色
小磁铁 | M3*4mm | 6 | 六角匙
吸盘 | M4*3.2cm螺杆 | 4 | 游标卡尺
滑动轴承 | GFM-0506-05 | 6
 | GFM-04050-04 | 12
螺丝 | M10*50 | 1
防松螺母 | M10 | 1
轴间螺丝 | M3*12 | 5
 | M3*30 | 2
 | M4*20 | 1
 | M4*30 | 1
圆柱头螺丝 | M3*12 | 8
自攻螺丝 | M3*12 | 8
一字塞打螺钉 | M3*12 | 1
 | M4*25 | 1
防滑螺母 | M3 | 8
 | M4 | 3
防滑螺母平底 | M3 | 4
舵机延长线 | 60芯 并线棕红橙 飞机种类：200mm | 2
 | 60芯 并线棕红橙 飞机种类：500mm | 1

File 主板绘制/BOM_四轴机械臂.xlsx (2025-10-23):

No. | Quantity | Comment | Designator | Value | Manufacturer Part | Manufacturer | Supplier Part | Supplier | Footprint | Mounting Style | Mounting Type
1 | 1 | 220uF | C1 | 220uF | RX220UF16V90RV0106 | KNSCHA(科尼盛) | C3445239 | LCSC | CAP-SMD_BD6.3-L6.6-W6.6-FD-2
2 | 1 | 100nF | C2 | 100nF | CL10B104KB8NNNC | SAMSUNG(三星) | C1591 | LCSC | C0603
3 | 2 | 10uF | C3,C5 | 10uF | MT18N1R5C500CT | 华新科(Walsin) | C96446 | LCSC | c0603
4 | 2 | 0.1uF | C4,C6 | 0.1uF | MT18N1R5C500CT | 华新科(Walsin) | C14663 | LCSC | c0603
5 | 1 | 1uF | C7 | 1uF | CL10A105KB8NNNC | SAMSUNG(三星) | C15849 | LCSC | C0603
6 | 1 | SS34 | D1 |  | SS34 | MDD | C8678 | LCSC | DO-214AC_L4.3-W2.7-LS5.3-RD
7 | 2 | 2.54-1*10P母 | J1,J2 |  | 2.54-1*10P母 | BOOMELE(博穆精密) | C35445 | LCSC | HDR-TH_10P-P2.54-V-F |  | 直插
8 | 1 | 19-217/GHC-YR1S2/3T | LED1 |  | 19-217/GHC-YR1S2/3T | EVERLIGHT(亿光) | C72043 | LCSC | LED0603-RD
9 | 2 | SS8050-H | Q1,Q2 |  | SS8050-H | YANGJIE(扬杰) | C699255 | LCSC | SOT-23-3_L2.9-W1.3-P1.90-LS2.4-BR
10 | 4 | 5.1kΩ | R1,R2,R3,R5 | 5.1kΩ | 0603WAF5101T5E | UNI-ROYAL(厚声) | C23186 | LCSC | R0603
11 | 1 | 100Ω | R4 | 100Ω | 0603 ±5% 100Ω | VO(翔胜) | C2889393 | LCSC | R0603
12 | 2 | 10kΩ | R6,R7 | 10kΩ | ERJ3EKF1002V | PANASONIC(松下) | C191124 | LCSC | R0603
13 | 1 | 1kΩ | R8 | 1kΩ | 0603WAF1001T5E | UNI-ROYAL(厚声) | C21190 | LCSC | R0603
14 | 1 | 10kΩ | R9 | 10kΩ | SG73P1JTTD1002F | KOA | C880254 | LCSC | r0603
15 | 1 | TS24CA | SW1 |  | TS24CA | SHOU HAN(首韩) | C393942 | LCSC | SW-SMD_TS24CA | 卧贴
16 | 1 | YTC-TC6-268 | U1 |  | YTC-TC6-268 | YIYUAN(怡远) | C5260484 | LCSC | TYPE-C-SMD_YIYUAN_YTC-TC6-268
17 | 1 | 20009-UCAF001-X | U2 |  | 20009-UCAF001-X | MINTRON(明硕) | C3148200 | LCSC | TYPE-C-SMD_20009-UCAF001-X
18 | 1 | DB125-3.81-3P-BK-S | U3 |  | DB125-3.81-3P-BK-S | DIBO(地博电气) | C881704 | LCSC | CONN-TH_DB125-3.81-3P-BK | 直针
19 | 1 | AMS1117-3.3 | U4 |  | AMS1117-3.3 | UMW(广东友台半导体) | C347222 | LCSC | SOT-223-4_L6.5-W3.5-P2.30-LS7.0-BR
20 | 1 | CH340C | U5 |  | CH340C | WCH(南京沁恒) | C84681 | LCSC | SOP-16_L10.0-W3.9-P1.27-LS6.0-BL
21 | 1 | ESP32-S | U6 |  | ESP32-S | Ai-Thinker(安信可) | C277944 | LCSC | wirelm-smd_esp32-s

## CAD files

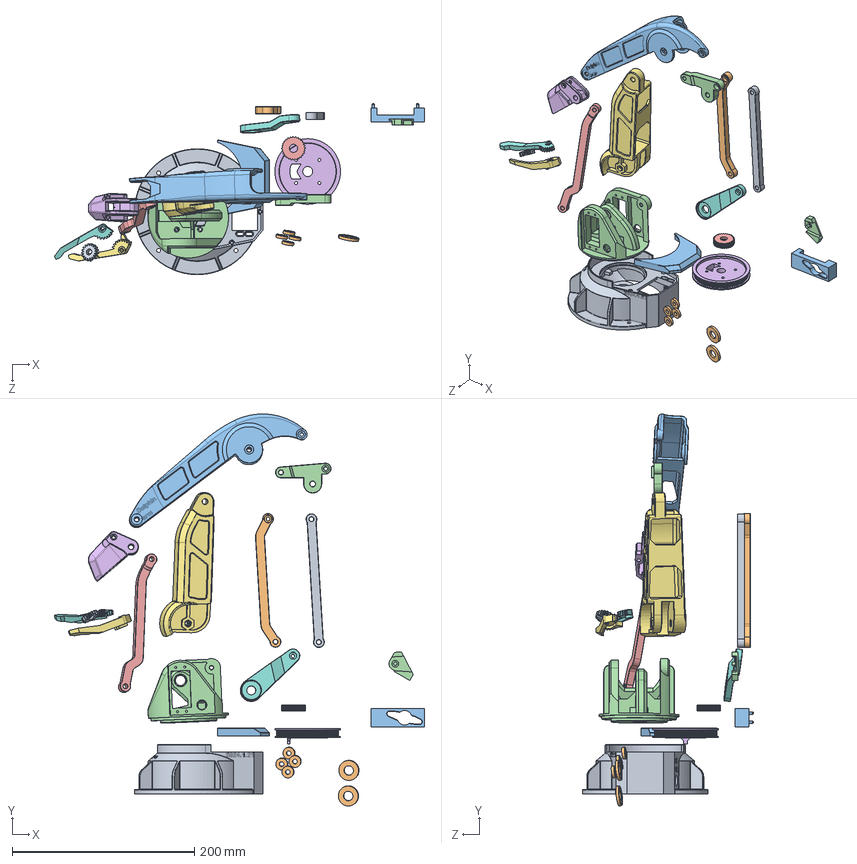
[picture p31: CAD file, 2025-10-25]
机械设计/海豚机械臂/3D打印件.SLDASM
406.0 x 429.9 x 187.9 mm
固定底座
B轴轴承压块 x 4
固定底座盖子
（15课程结束时保存）（答案）旋转底座
HTPA28S3M060_A_H5_b
HTPA72S3M060_A_H8_b
（15课程结束时保存）（答案）BC连杆
（15课程结束时保存）（答案）C轴摇杆
C轴连杆
下水平连杆
CD连杆
三角形连杆
上水平连杆
夹爪支架
上手指齿轮组合
下手指齿轮组合
主动齿
A轴轴承压块 x 2
(29课最后保存）（答案）19-B轴舵机舵盘定位块
(29课最后保存）（答案）20-C轴舵机舵盘定位块

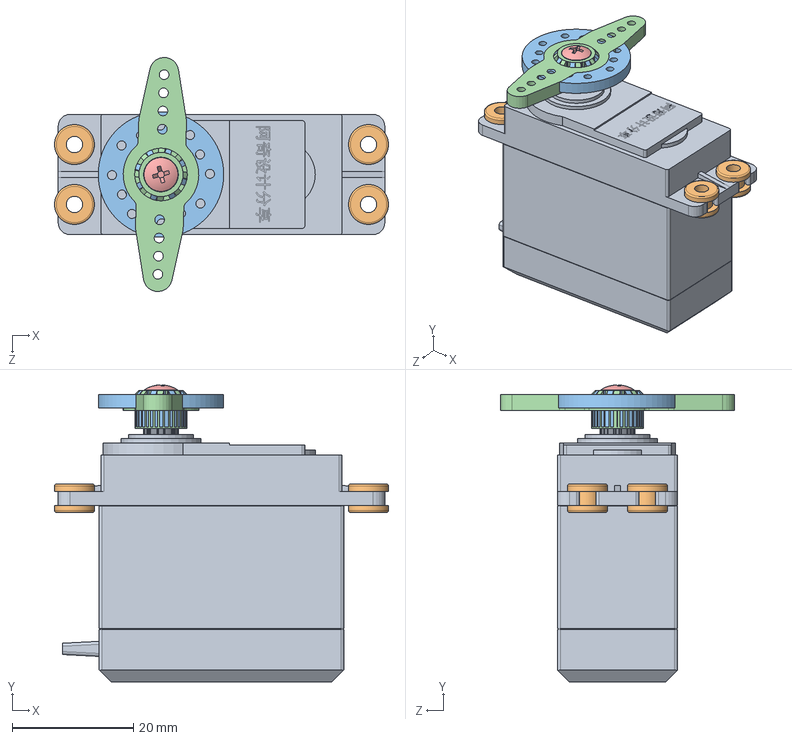
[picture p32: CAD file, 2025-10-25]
机械设计/固定底座/大舵机装配体[阿奇设计分享提供]2018.SLDASM
55.2 x 49.1 x 38.7 mm
大舵机渲染2018
舵机橡胶圈渲染2018 x 4
舵机圆舵盘渲染2018
cross recessed pan head screws gb(GB_CROSS_SCREWS_TYPE1 M3X6-6 H type-N)2018

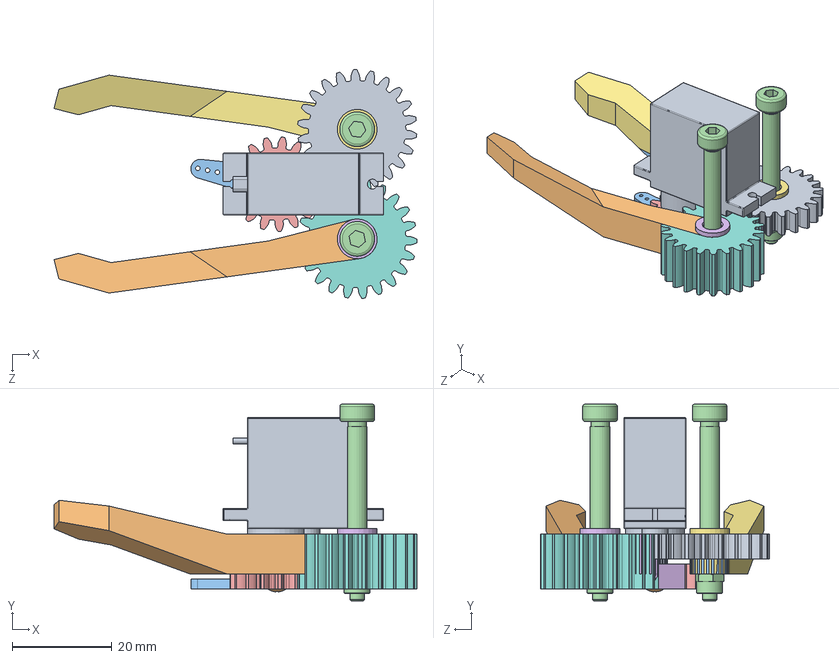
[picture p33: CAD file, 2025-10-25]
机械设计/夹爪机构/夹爪完全体.SLDASM
72.9 x 39.5 x 46.0 mm
MG90S 金属舵机渲染2018
cross recessed pan head screws gb(GB_CROSS_SCREWS_TYPE1 M2X4-4 H type-N)2018
MG90S 金属舵机单舵臂渲染2018
￠4×M3×30 轴肩螺丝 2018 x 2
主动齿
上手指齿轮组合
下手指齿轮组合
GB／T6172．2-2000非金属嵌件六角锁紧薄螺母3 x 2

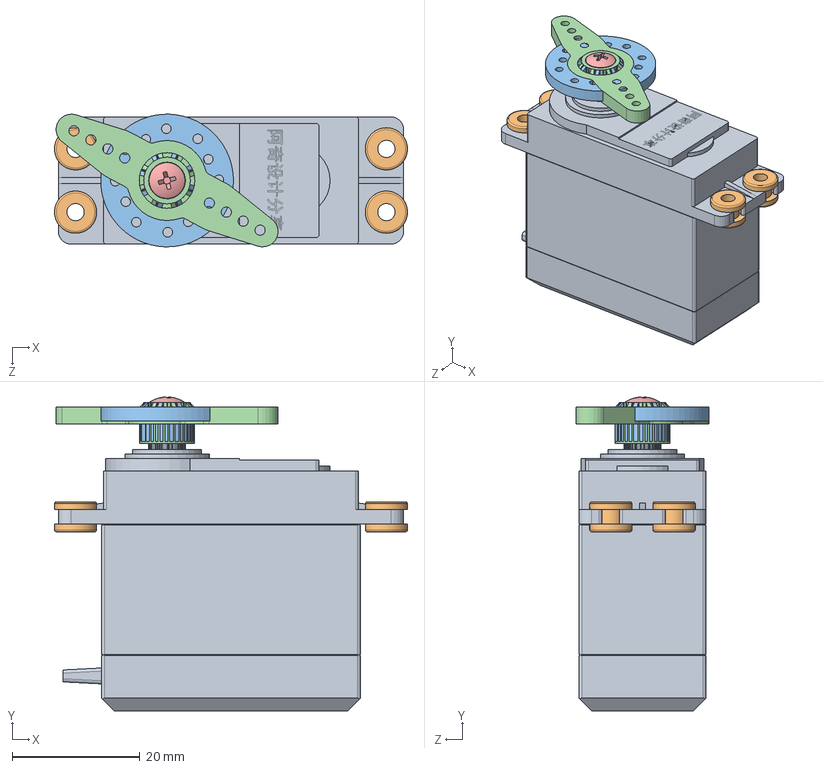
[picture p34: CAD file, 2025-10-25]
机械设计/旋转底座/（15课程结束时保存）（答案）大舵机装配体[阿奇设计分享提供]2018.SLDASM
55.2 x 49.1 x 20.8 mm
（16课程结束时保存）（答案）大舵机渲染2018
（16课程结束时保存）（答案）舵机橡胶圈渲染2018 x 4
（16课程结束时保存）（答案）舵机圆舵盘渲染2018
（16课程结束时保存）（答案）舵机单臂舵盘渲染2018
（16课程结束时保存）（答案）cross recessed pan head screws gb(GB_CROSS_SCREWS_TYPE1 M3X6-6 H type-N)2018

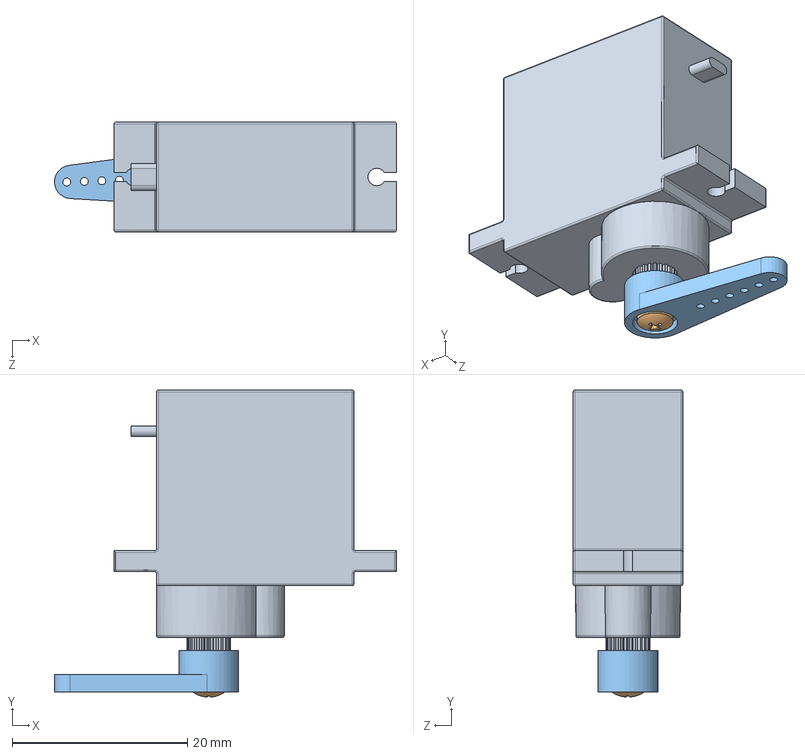
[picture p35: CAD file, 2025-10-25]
机械设计/夹爪机构/MG90S 金属舵机装配体 2018.SLDASM
39.0 x 35.0 x 12.5 mm
MG90S 金属舵机渲染2018
cross recessed pan head screws gb(GB_CROSS_SCREWS_TYPE1 M2X4-4 H type-N)2018
MG90S 金属舵机单舵臂渲染2018

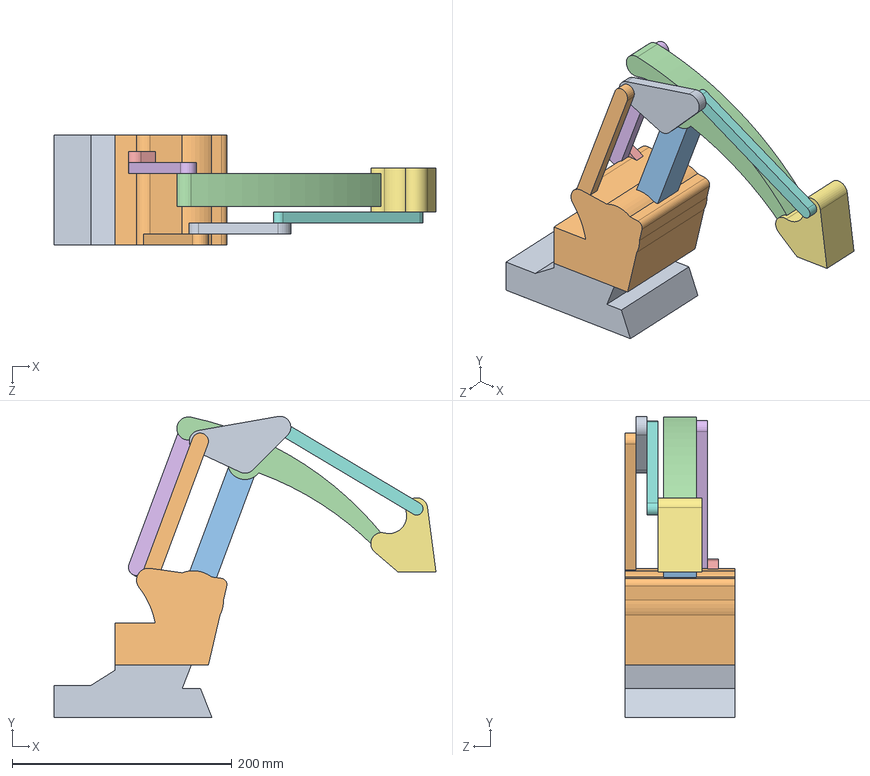
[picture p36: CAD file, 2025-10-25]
逆向工程/ABB-irb-460逆向工程/ABB-irb-460逆向工程.SLDASM
348.0 x 274.6 x 100.0 mm
（课程结束时保存）（答案）方案-固定底座
（课程结束时保存）（答案）方案-旋转底座
（课程结束时保存）（答案）方案-BC连杆
（课程结束时保存）（答案）方案-CD连杆
（课程结束时保存）（答案）方案-C轴摇杆
（课程结束时保存）（答案）方案-C轴连杆
（课程结束时保存）（答案）方案-D轴支架
（课程结束时保存）（答案）0606L1
（课程结束时保存）（答案）方案-三角形连杆
（课程结束时保存）（答案）0606L2

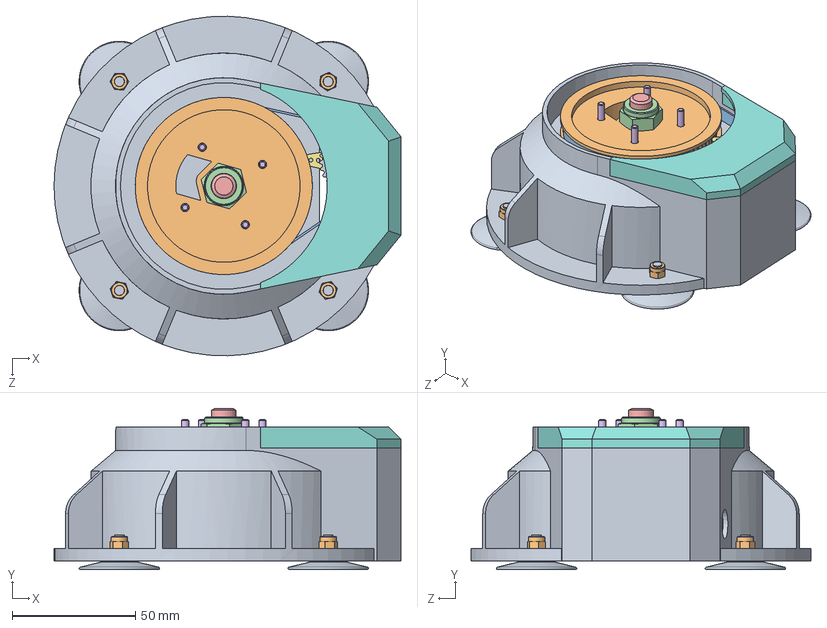
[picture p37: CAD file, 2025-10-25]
机械设计/固定底座/固定底座完全体.SLDASM
141.0 x 65.5 x 138.0 mm
固定底座
GB／T276-94深沟球轴承61900
GB／T276-94深沟球轴承61809
大舵机渲染2018
舵机橡胶圈渲染2018 x 4
舵机圆舵盘渲染2018
cross recessed pan head screws gb(GB_CROSS_SCREWS_TYPE1 M3X6-6 H type-N)2018
HTPA28S3M060_A_H5_b
HTPA72S3M060_A_H8_b
HTBN264S3M_60_info_1_28_72
GB／T889．1-20001型非金属嵌件六角锁紧螺母M10
GB／T70．1-2000内六角圆柱头螺钉M10×50
GB／T70．1-2000内六角圆柱头螺钉M3×12 x 8
GB／T6172．2-2000非金属嵌件六角锁紧薄螺母3 x 4
固定底座盖子
M4 吸盘（2018） x 4
（15课程结束时保存）（答案）GB／T6172．2-2000非金属嵌件六角锁紧薄螺母4 x 4

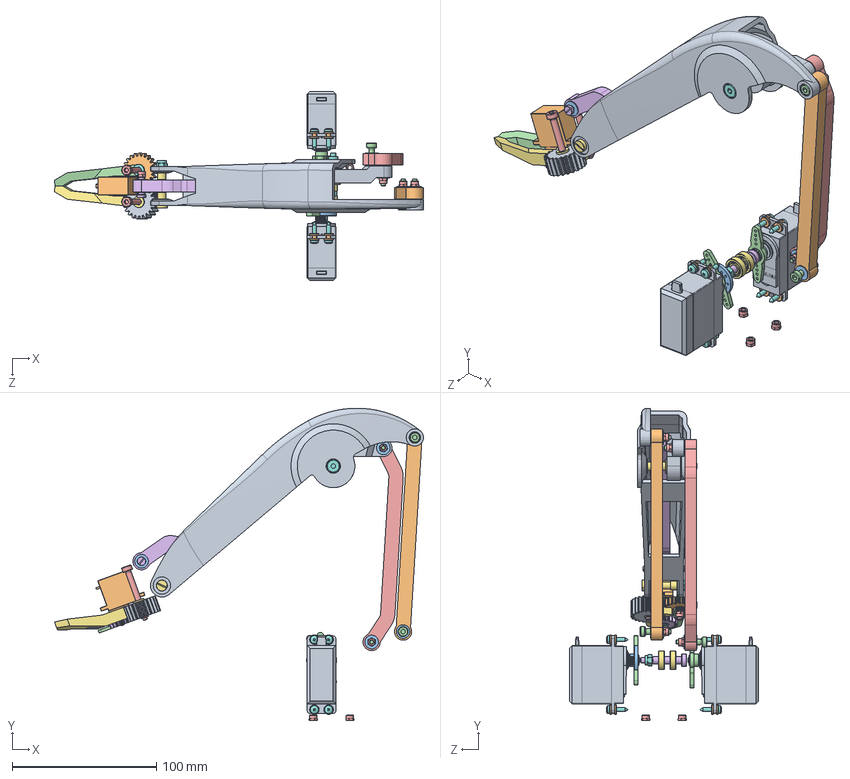
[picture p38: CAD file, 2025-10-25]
机械设计/旋转底座/旋转底座完全体.SLDASM
256.1 x 216.9 x 131.4 mm
（16课程结束时保存）（答案）大舵机渲染2018 x 2
（16课程结束时保存）（答案）舵机橡胶圈渲染2018 x 8
（16课程结束时保存）（答案）舵机圆舵盘渲染2018
（16课程结束时保存）（答案）cross recessed pan head screws gb(GB_CROSS_SCREWS_TYPE1 M3X6-6 H type-N)2018 x 2
（16课程结束时保存）（答案）舵机单臂舵盘渲染2018
（15课程结束时保存）5×M4×20 轴肩螺丝2018
（15课程结束时保存）（答案）GB／T276-94深沟球轴承619／5 x 2
（15课程结束时保存）（答案）GB／T6172．2-2000非金属嵌件六角锁紧薄螺母4 x 3
CD连杆
MG90S 金属舵机渲染2018
cross recessed pan head screws gb(GB_CROSS_SCREWS_TYPE1 M2X4-4 H type-N)2018
MG90S 金属舵机单舵臂渲染2018
￠4×M3×30 轴肩螺丝 2018 x 2
主动齿
上手指齿轮组合
下手指齿轮组合
GB／T6172．2-2000非金属嵌件六角锁紧薄螺母3 x 12
上水平连杆
易格斯轴承GFM-0506-05 2018 x 6
￠5×M4×30 轴肩螺丝渲染 2018
三角形连杆
C轴连杆
易格斯轴承GFM-04050-04 2018 x 12
￠4×M3×12 轴肩螺丝 2018 x 5
下水平连杆
一字槽塞打螺钉 M3×12 2018
一字槽塞打螺钉 M4×25 2018
GB845-1985十字槽盘头自攻螺钉-C型ST2．9×13 x 8

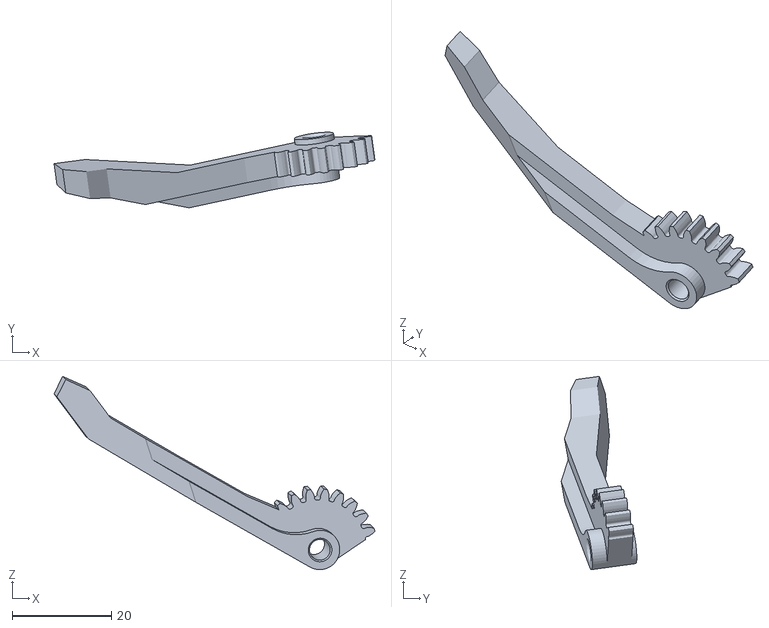
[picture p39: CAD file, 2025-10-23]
机械设计/3D打印零件/3D打印件 - 下手指齿轮组合-4.STL
64.6 x 15.2 x 38.9

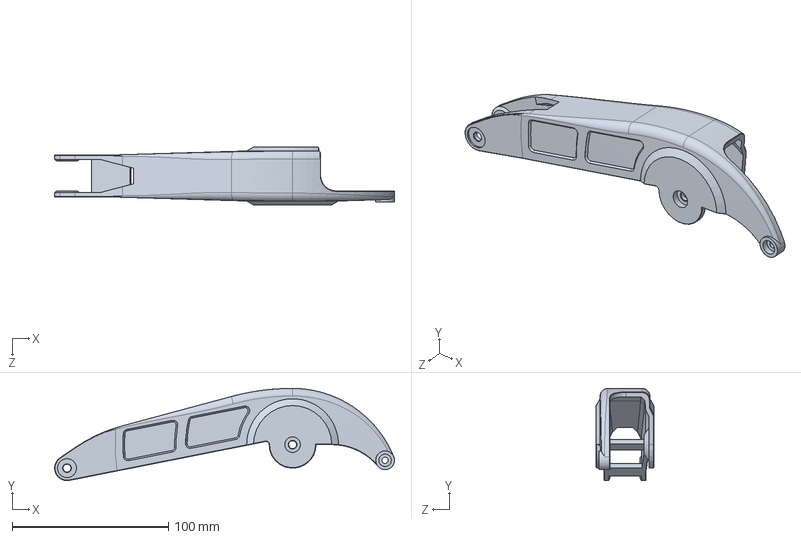
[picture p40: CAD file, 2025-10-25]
机械设计/C轴与连杆机构/CD连杆.SLDPRT
217.4 x 59.0 x 37.0 mm

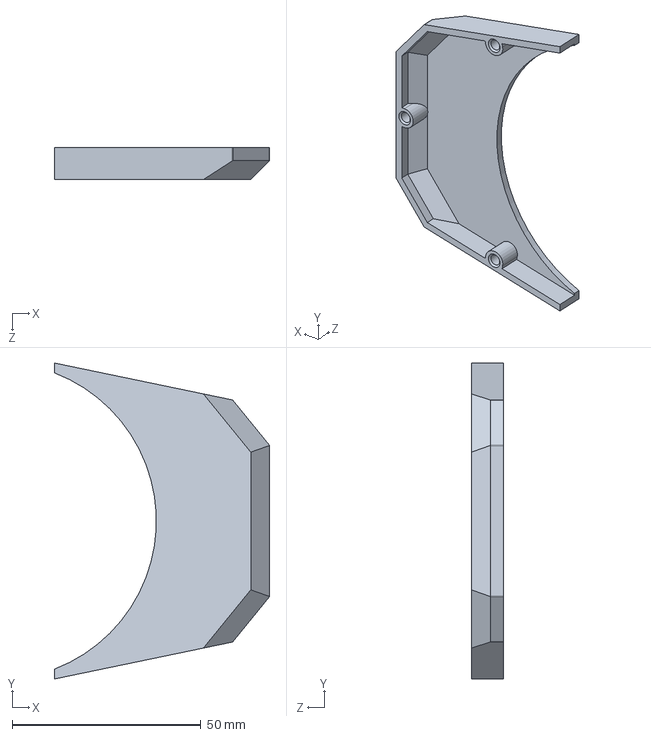
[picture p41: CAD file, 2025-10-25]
机械设计/固定底座/固定底座盖子.SLDPRT
57.0 x 83.7 x 8.50 mm

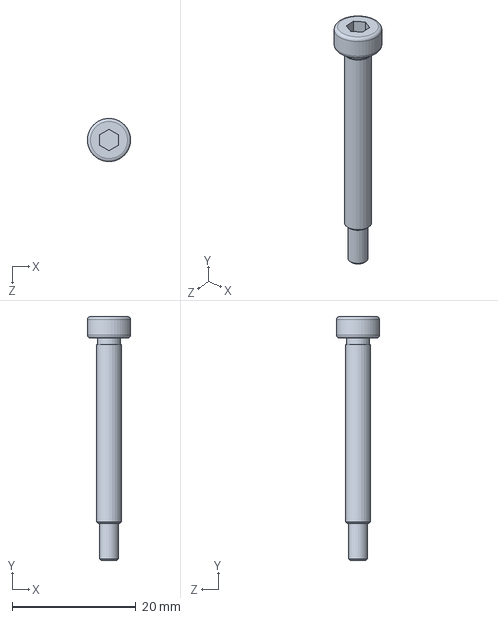
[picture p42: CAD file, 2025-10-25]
机械设计/夹爪机构/￠4×M3×30 轴肩螺丝 2018.SLDPRT
7.00 x 39.5 x 6.98 mm

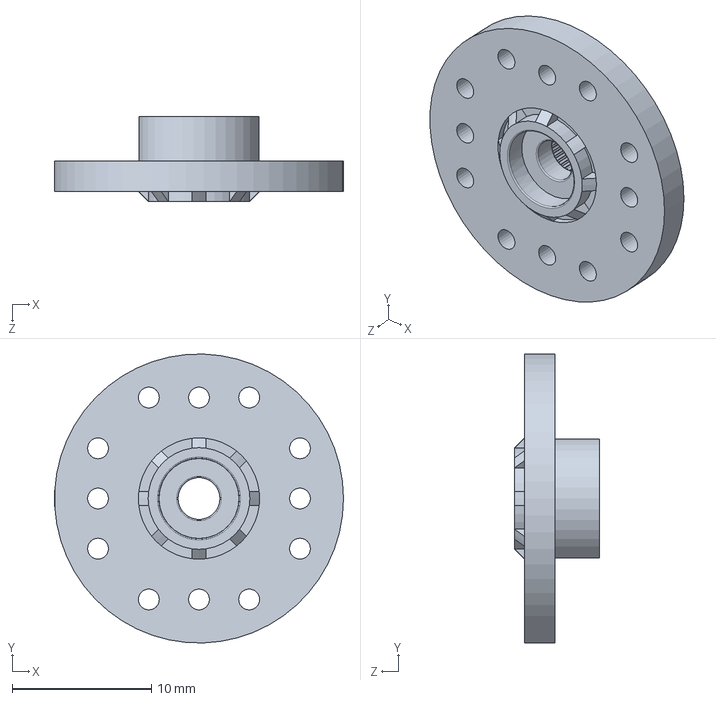
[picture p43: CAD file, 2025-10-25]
机械设计/旋转底座/（16课程结束时保存）舵机圆舵盘渲染2018.sldprt
20.8 x 20.7 x 6.10 mm

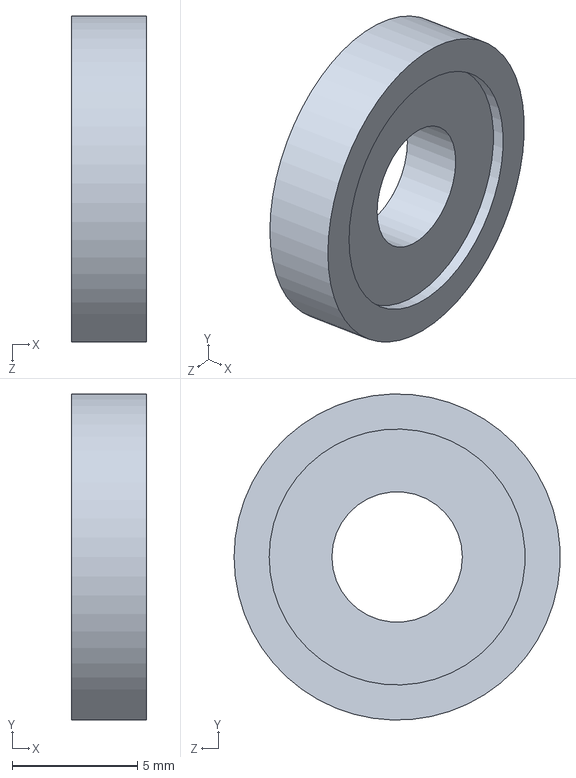
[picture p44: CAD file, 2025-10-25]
机械设计/海豚机械臂/A轴轴承压块.SLDPRT
3.00 x 13.0 x 13.0 mm

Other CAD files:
机械设计/旋转底座/（16课程结束时保存）大舵机装配体[阿奇设计分享提供]2018.SLDASM
逆向工程/ABB-irb-460逆向工程/（课程结束时保存）（答案）机械臂草图模拟.SLDPRT
机械设计/3D打印零件/3D打印件 - 上手指齿轮组合-4.STL
机械设计/C轴与连杆机构/￠4×M3×12 轴肩螺丝 2018.SLDPRT
机械设计/3D打印零件/3D打印件 - (29课最后保存）（答案）19-B轴舵机舵盘定位块-1.STL
机械设计/3D打印零件/3D打印件 - (29课最后保存）（答案）20-C轴舵机舵盘定位块-1.STL
机械设计/3D打印零件/3D打印件 - A轴轴承压块-1.STL
机械设计/3D打印零件/3D打印件 - A轴轴承压块-2.STL
机械设计/3D打印零件/3D打印件 - B轴轴承压块-1.STL
机械设计/3D打印零件/3D打印件 - B轴轴承压块-2.STL
机械设计/3D打印零件/3D打印件 - B轴轴承压块-3.STL
机械设计/3D打印零件/3D打印件 - B轴轴承压块-4.STL
机械设计/3D打印零件/3D打印件 - CD连杆-1.STL
机械设计/3D打印零件/3D打印件 - C轴连杆-1.STL
机械设计/3D打印零件/3D打印件 - HTPA28S3M060_A_H5_b-1.STL
机械设计/3D打印零件/3D打印件 - HTPA72S3M060_A_H8_b-1.STL
机械设计/3D打印零件/3D打印件 - 三角形连杆-1.STL
机械设计/3D打印零件/3D打印件 - 上水平连杆-1.STL
机械设计/3D打印零件/3D打印件 - 下水平连杆-1.STL
机械设计/3D打印零件/3D打印件 - 主动齿-2.STL
机械设计/3D打印零件/3D打印件 - 固定底座-1.STL
机械设计/3D打印零件/3D打印件 - 固定底座盖子-1.STL
机械设计/3D打印零件/3D打印件 - 夹爪支架-1.STL
机械设计/3D打印零件/3D打印件 - （15课程结束时保存）（答案）BC连杆-1.STL
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

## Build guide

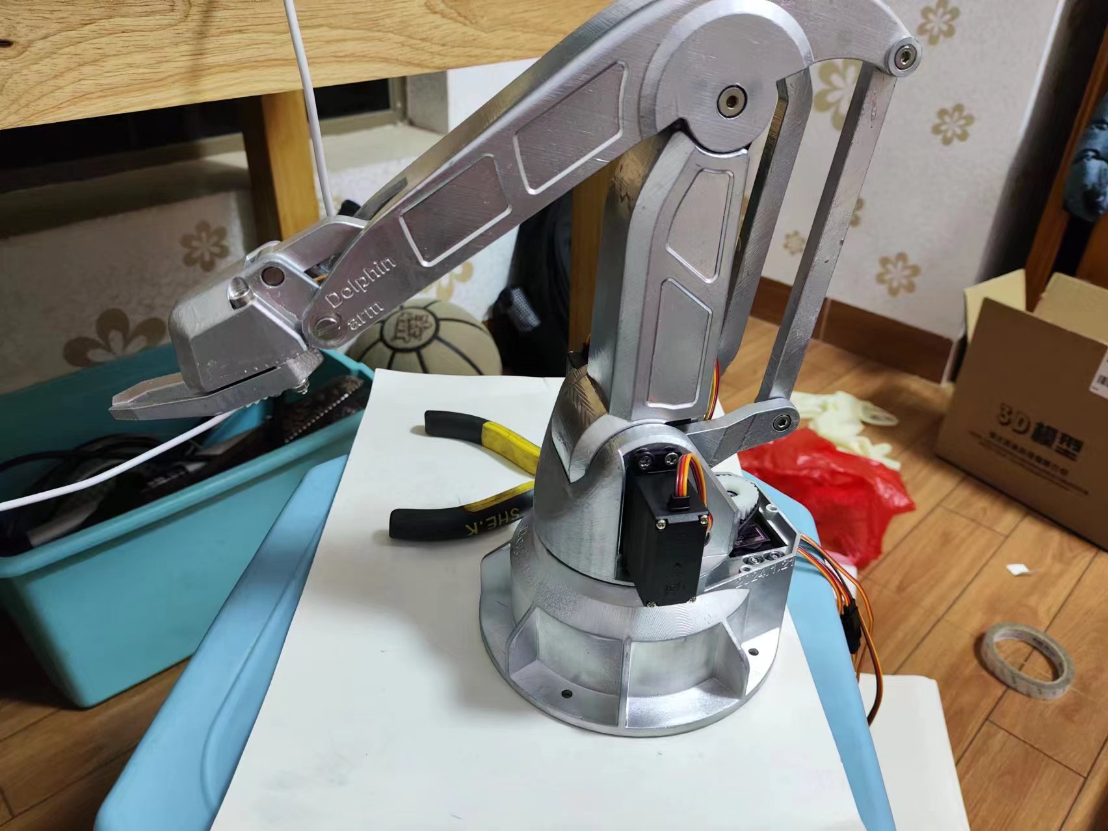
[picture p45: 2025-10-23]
制作过程纪念/组装完全体.jpg

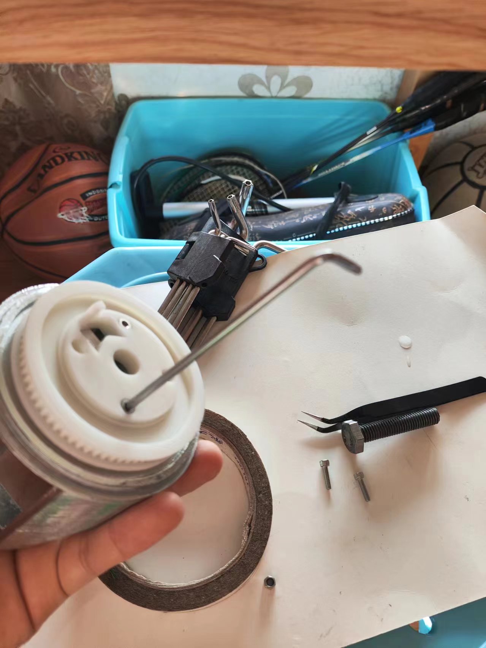
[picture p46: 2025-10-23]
制作过程纪念/机械臂组装2.jpg

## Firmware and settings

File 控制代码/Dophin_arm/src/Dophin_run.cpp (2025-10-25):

#include <Arduino.h>
#include <ESP32Servo.h>               //引入舵机标准库函数
#include <Ticker.h>

#define PIN_SERVO_A 21
#define PIN_SERVO_B 22
#define PIN_SERVO_C 23
#define PIN_SERVO_G 19        

struct SERVO                     //定义舵机结构体变量
{
    Servo engine[4];             //定义舵机变量
    uint8_t now[4];              //定义舵机当前角度   
    uint8_t set[4];              //定义舵机设置角度
};

SERVO servo_engine;               
Ticker timer;

void Servo_Init()                //定义舵机初始化函数
{
    uint8_t x;
    for(x = 0;x < 4;x ++)
    {
        servo_engine.engine[x].setPeriodHertz(50);             //初始化舵机频率
    }
    servo_engine.engine[0].attach(PIN_SERVO_A,500,2500);
    servo_engine.engine[1].attach(PIN_SERVO_B,500,2500);
    servo_engine.engine[2].attach(PIN_SERVO_C,500,2500);
    servo_engine.engine[3].attach(PIN_SERVO_G,500,2500);       
    Serial.printf("Servos are ready for 500,2500 us with 50Hz\n");

}

void Servo_back()               //定义舵机归位函数
{
    servo_engine.now[0] = 90;
    servo_engine.set[0] = 90;
    servo_engine.engine[0].write(90);

    servo_engine.now[1] = 0;
    servo_engine.set[1] = 0;
    servo_engine.engine[1].write(0);

    servo_engine.now[2] = 150;
    servo_engine.set[2] = 150;
    servo_engine.engine[2].write(150);

    servo_engine.now[3] = 0;
    servo_engine.set[3] = 0;
    servo_engine.engine[3].write(0);

    Serial.printf("Servos back\n");
}

void timer_speed(uint8_t x)        //舵机速度控制函数，原理是利用定时器定时功能，每隔一段时间进行一次角度判断函数
{
    void timer_back();

    timer.attach_ms(x,timer_back);            //在规定时间重复执行定时器任务
    Serial.printf("The speed delay is %d\n",x);
}

void timer_back()                       //定义舵机now修正函数
{
    uint8_t Servo_run(uint8_t x,uint8_t set_angle,uint8_t now_angle);

    uint8_t x;
    for(x = 0;x < 4;x ++)                 //在舵机运动到指定位置后，修正now为当前值，避免一直运动
    {
        servo_engine.now[x] = Servo_run(x,servo_engine.set[x],servo_engine.now[x]);
    }
}

uint8_t Servo_run(uint8_t x,uint8_t set_angle,uint8_t now_angle)         //定义舵机驱动函数，当set和now不同时，舵机驱动
{
    if(set_angle > now_angle)
    {
        servo_engine.engine[x].write(now_angle);
        now_angle++;
    }
    else if(set_angle < now_angle)
    {
        servo_engine.engine[x].write(now_angle);
        now_angle--;
    }
    return now_angle;                                     
}

void Servo_motor_run(uint8_t a,uint8_t b,uint8_t c,uint8_t d)         //定义多舵机控制函数，给set值
{
    servo_engine.set[0] = a;
    servo_engine.set[1] = b;
    servo_engine.set[2] = c;
    servo_engine.set[3] = d;
    Serial.printf("Order:ServoA %d ServoB %d ServoC %d ServoG %d\n",a,b,c,d);

}

void Servo_motor_to(uint8_t x,uint8_t y)         //定义单舵机驱动控制函数
{
    servo_engine.engine[x].write(y);
    servo_engine.now[x] = y;
    servo_engine.set[x] = y;
    Serial.printf("Servo%d has been %d\n",x,y);
}

void BLE_motor_run(uint8_t *angle)        //定义BLE蓝牙驱动函数
{
    uint8_t x;
    for(x = 0;x < 4;x ++)
    {
        servo_engine.set[x] = angle[x];
    }
}

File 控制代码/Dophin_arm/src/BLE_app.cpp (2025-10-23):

#include <Arduino.h>
#include "Dophin_run.h"

#include <BLEDevice.h>
#include <BLE2902.h>              //引进相关蓝牙通讯协议

#define SERVICE_UUID "4fafc201-1fb5-459e-8fcc-c5c9c331914b"
#define CHARACTERISTIC_UUID "beb5483e-36e1-4688-b7f5-ea07361b26a8"       //完整的128位UUID码

BLECharacteristic *pCharacteristic = NULL;            //创建特征Characteristic
bool bleConnected = false;                            //定义布尔型变量用于判断蓝牙是否连接

class bleServerCallbacks : public BLEServerCallbacks                     //Server回调函数声明
{
    void onConnect(BLEServer *pServer)
    {
        bleConnected = true;
        Serial.printf("现在有设备接入~");
    }

    void onDisconnect(BLEServer *pServer)
    {
        bleConnected = false;
        Serial.printf("现在有设备断开连接~");
        
        pServer->startAdvertising(); 
    }   // 在有设备接入后Advertising广播会被停止，所以要在设备断开连接时重新开启广播,不然的话只有重启ESP32后才能重新搜索到
};

class bleCharacteristicCallbacks : public BLECharacteristicCallbacks      //客户端回调函数声明
{
    void onRead(BLECharacteristic *pCharacteristic)            // 客户端读取事件回调函数
    { 
        Serial.printf("触发读取事件");
    }

    void onWrite(BLECharacteristic *pCharacteristic)           // 客户端写入事件回调函数
    { 
        size_t length = pCharacteristic->getLength();
        uint8_t *pdata = pCharacteristic->getData();
        int x;
        if(length == 8){
            if(pdata[0] == 0xA5 && pdata[1] == 0xA5 && pdata[2] == 0x01 ){
                //自定义接受数据协议0xA5 0xA5 0x01 angle1 angle2 angle3 angle4        
                BLE_motor_run(pdata+3);
            }
        }
        for (x = 0; x < length; x++)
        {
            Serial.printf(" %d\n", pdata[x]);
        }
    }
};

void BLE_Init()                   //定义初始化蓝牙函数
{
    BLEDevice :: init("Mini-Arm");                 //创建BLE蓝牙设备，初始化蓝牙功能
    BLEServer *pServer = BLEDevice::createServer();      //创建服务器，设置设备的模式为BLE Server
    pServer->setCallbacks(new bleServerCallbacks());       //绑定回调函数

    BLEService *pService = pServer->createService(SERVICE_UUID);         //创建服务，给Server添加一个Service
    pCharacteristic = pService->createCharacteristic(            
        CHARACTERISTIC_UUID,
        BLECharacteristic::PROPERTY_READ |
            BLECharacteristic::PROPERTY_NOTIFY |
            BLECharacteristic::PROPERTY_WRITE);     //为Serveice创建Characteristic，并且声明该特征的属性为可读可写可申报
    
    pCharacteristic->setCallbacks(new bleCharacteristicCallbacks());    //如有客户端发送数据，自动执行回调函数
    pCharacteristic->addDescriptor(new BLE2902());  // 添加描述  

    pService->start(); // 启动服务
    BLEDevice :: startAdvertising();               //开启advertising广播                 

}
